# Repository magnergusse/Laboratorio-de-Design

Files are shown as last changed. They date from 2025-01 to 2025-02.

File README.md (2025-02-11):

# Laboratorio-de-Design

[PT] Nesta unidade curricular, o objetivo foi a concepção de um braço robótico para uma missão espacial, cuja definição, incluindo objetivos, requisitos e métricas envolvidas, foi proposta pelo grupo. O projeto CAD do braço robótico foi desenvolvido e concluído com sucesso.

[EN] In this course, the objective was to design a robotic arm for a space mission, with the mission details, including objectives, requirements, and involved metrics, proposed by the group. The CAD design of the robotic arm was developed and successfully completed.

<h2>Gallery</h2>
<p align="center">

<table>
  <tr>
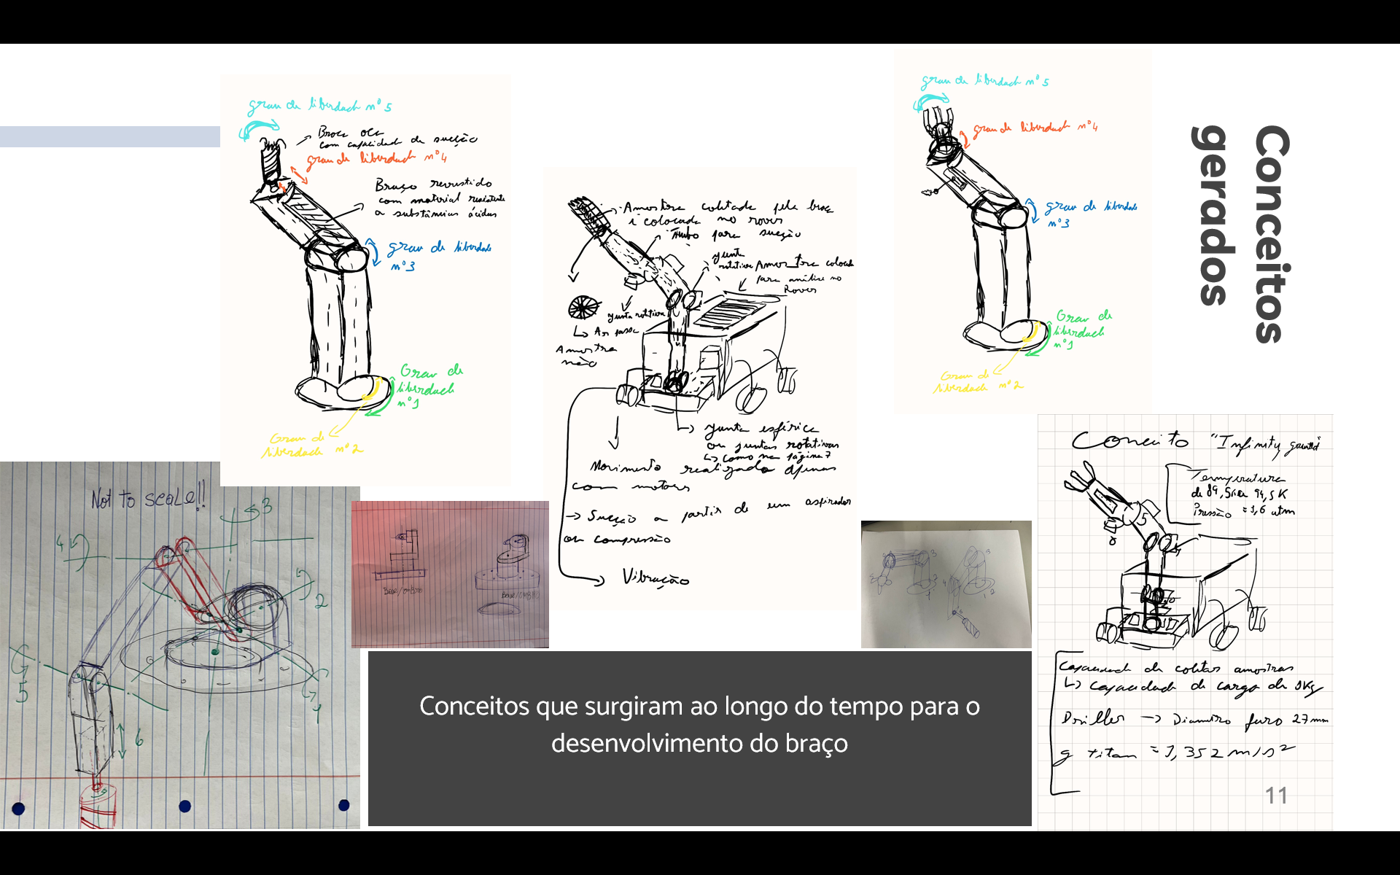
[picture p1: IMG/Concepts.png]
    <td></td>
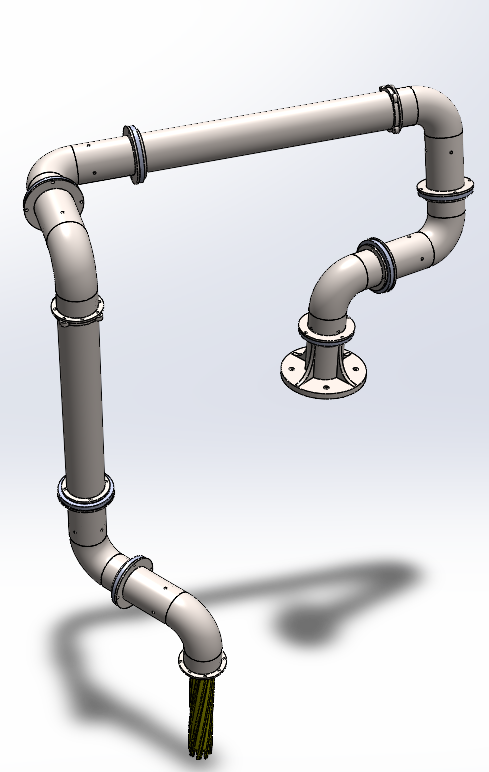
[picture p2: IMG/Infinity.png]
    <td rowspan="2"></td>
  </tr>
  <tr>
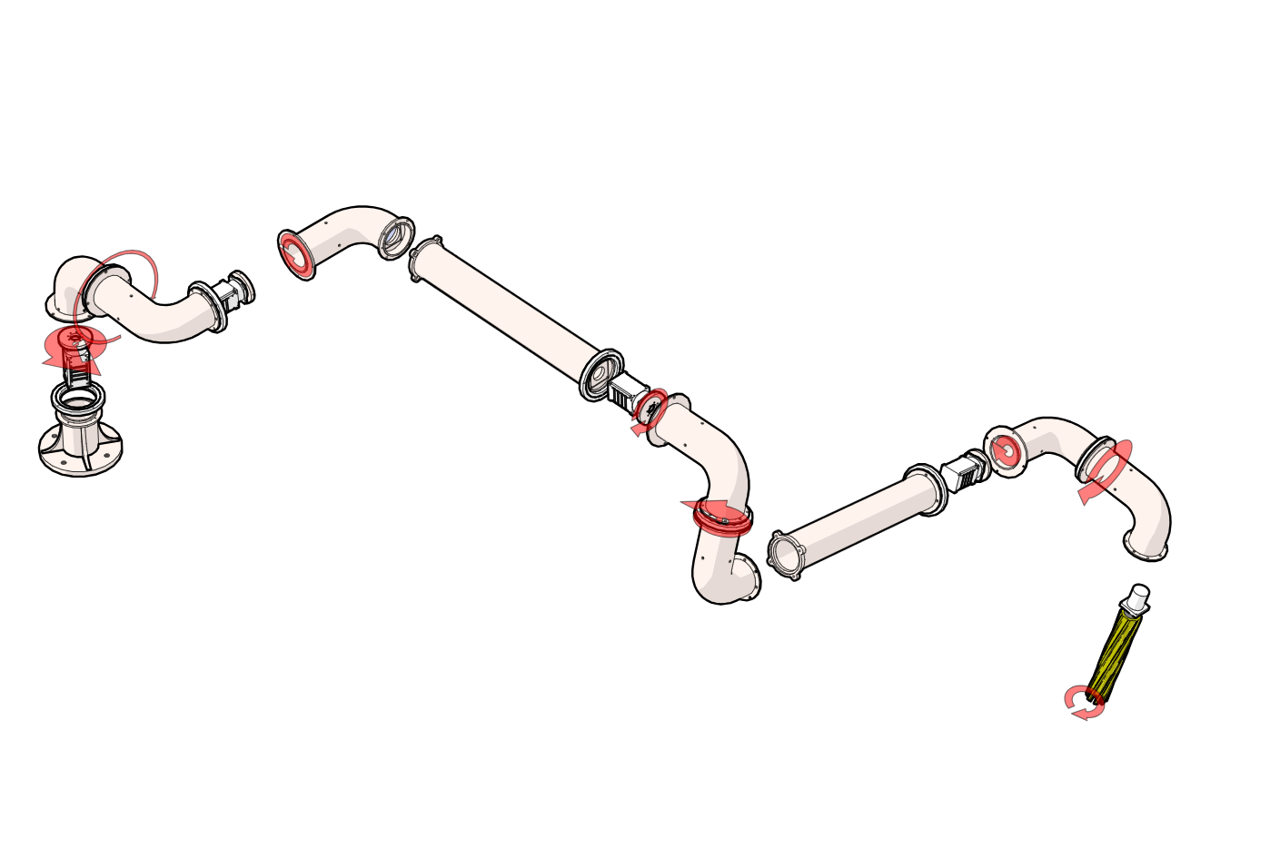
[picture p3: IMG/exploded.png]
    <td></td>
  </tr>
</table>
</p>

<p align="center">
<table>
  <tr>
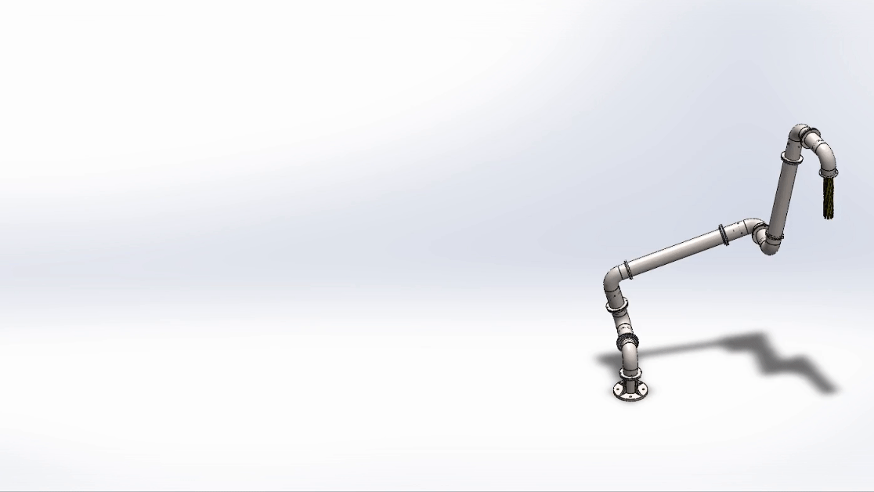
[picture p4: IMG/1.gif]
    <td></td>
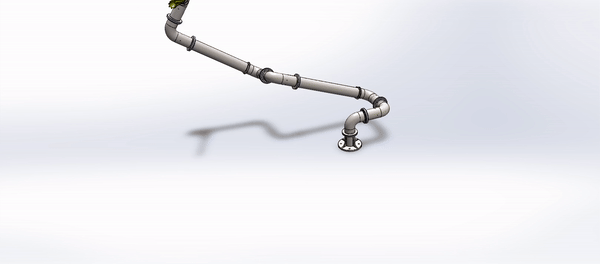
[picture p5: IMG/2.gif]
    <td></td>
  </tr>
<tr>
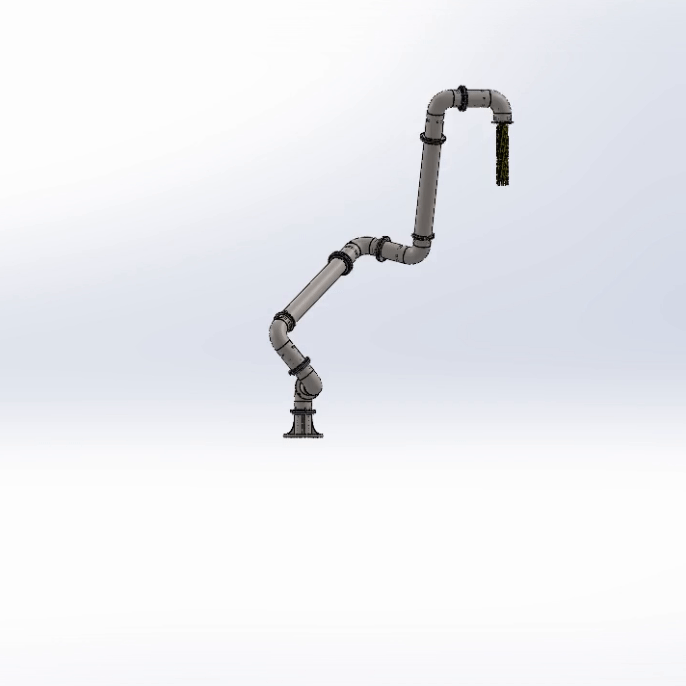
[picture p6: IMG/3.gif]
    <td></td>
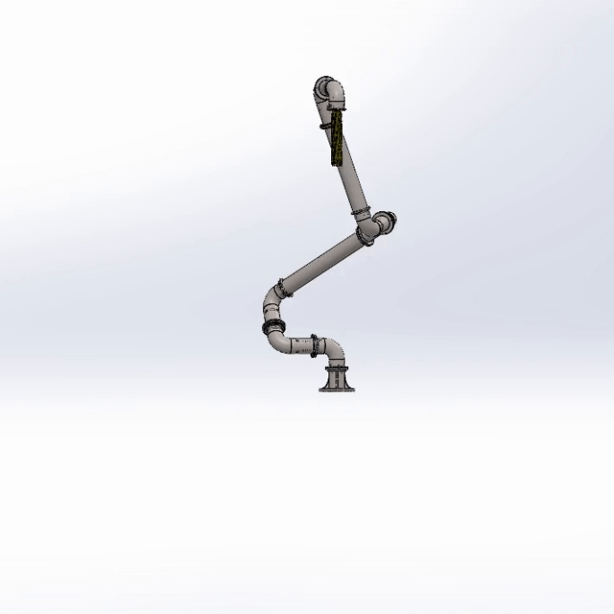
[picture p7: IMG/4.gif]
    <td></td>
</tr>

</table>

 </p>

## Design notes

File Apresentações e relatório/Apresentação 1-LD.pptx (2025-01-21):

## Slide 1

Braço Robótico: Infinity Gauntlet

Apresentação 1
17/10/2023

Grupo:
108217 – Diogo Ribeiro
110180 – Magner Gusse

## Mission Statement

Product description:
- Braço robótico com capacidade de furar o solo e fazer um pick & collect em titã.
Key Goals:
- Estudo da possibilidade de colonização do planeta, mineração do planeta.
Primary Market:
- Comunidade científica.

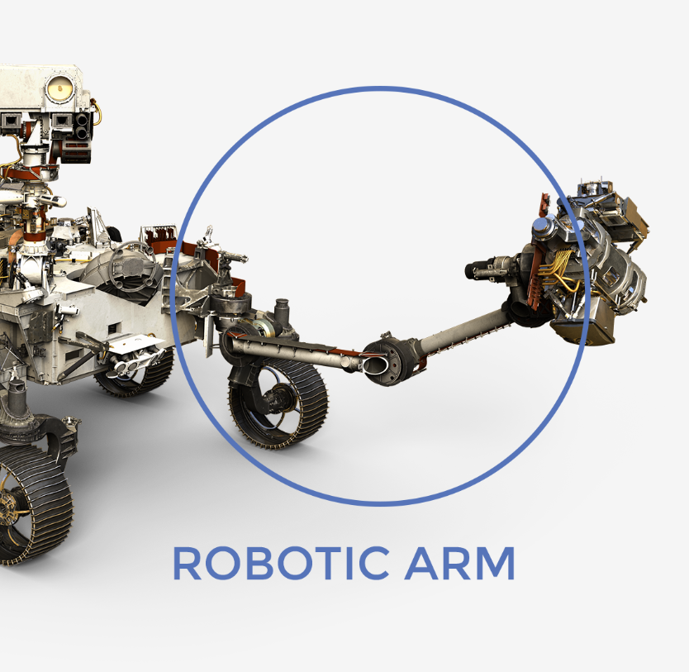
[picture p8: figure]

## Mission Statement

Secondary Markets:
- Comunidade geral.
- Empresas energéticas
Assumptions:
- Resistir às propriedades climatéricas de Titã.
- Acoplavél ao Rover.
- Recorre a mesma fonte energética do Rover.
- 5 graus de liberdade.
- Capaz de fazer furos e coletar amostras.

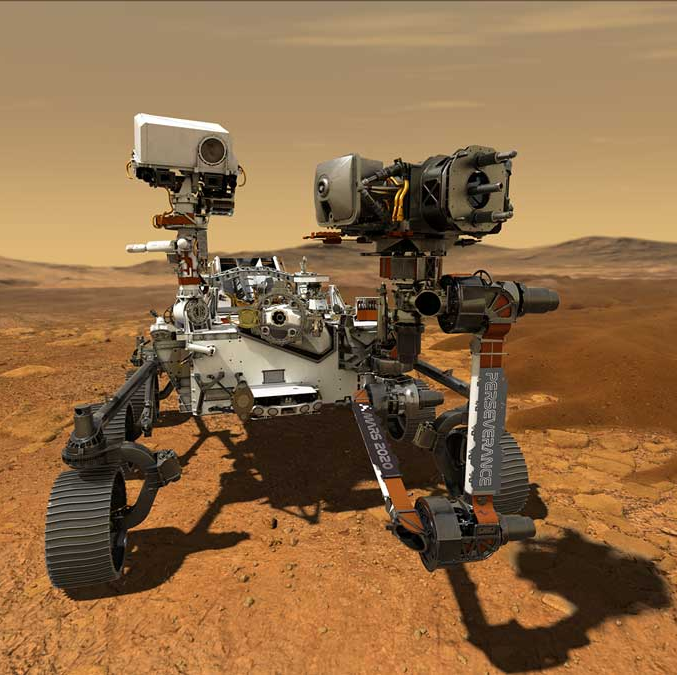
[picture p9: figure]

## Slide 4

Requisitos e especificações

Requisitos | Especificações
Acoplamento ao Rover simples | Feito em 30 minutos
Controlo Remoto | Ligação a 1,2 milhões de quilómetros da Terra
Resistência às propriedades climatéricas | Temperaturas entre 89,5 K e 94,5K
Resistência à pressão atmosférica | Pressão atmosférica de 1,6 atm
Coleção de amostras | Capacidade de carga de pelo menos 3 Kg
Furar a superfície | Furos de 40 mm de diâmetro e 70mm de profundidade
Adapta-se ao campo gravítico | Titã apresenta uma aceleração gravítica de 1,352 m/s²
Capacidade de realizar várias operações | 5 graus de liberdade
Duração total | Tempo de vida de 10 anos
Necessidade de pouca manutenção | Manutenção apenas uma vez ao fim de 5 anos

## Geração de Conceitos

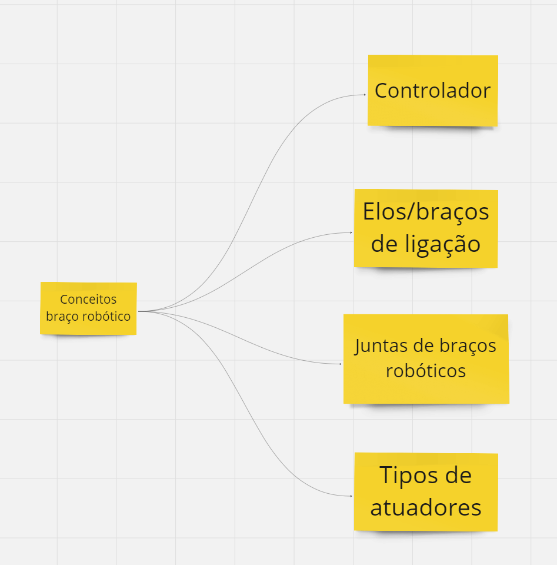
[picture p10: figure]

## Controladores

- Controladores Industriais
- Robustos e Confiáveis
- Suportam cargas pesadas
- Resistentes a Condições ambientais adversas
- Controladores de motores elétricos
- Correspondem a nossa necessidade de alto desempenho

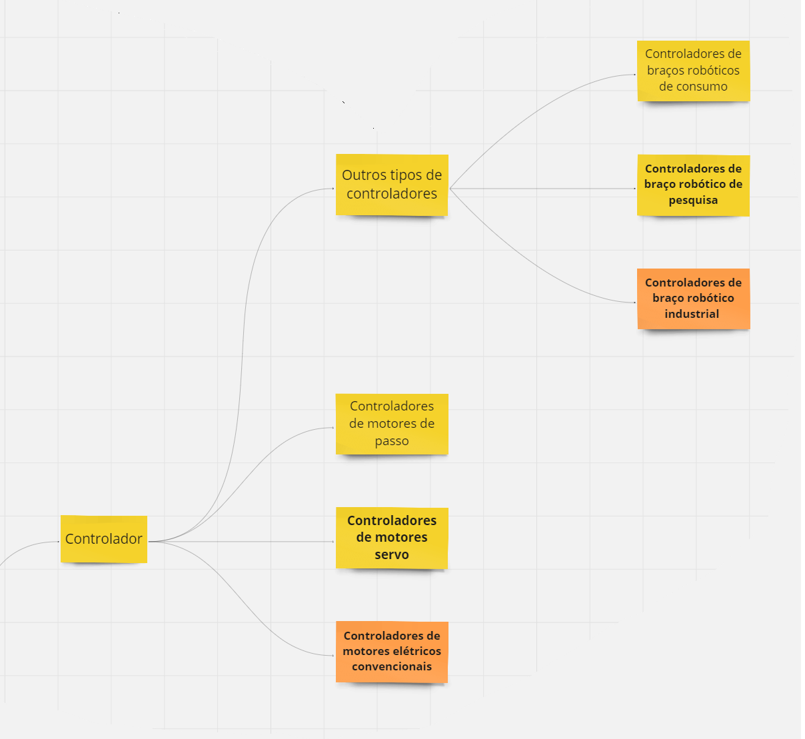
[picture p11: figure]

## Elementos de Ligação

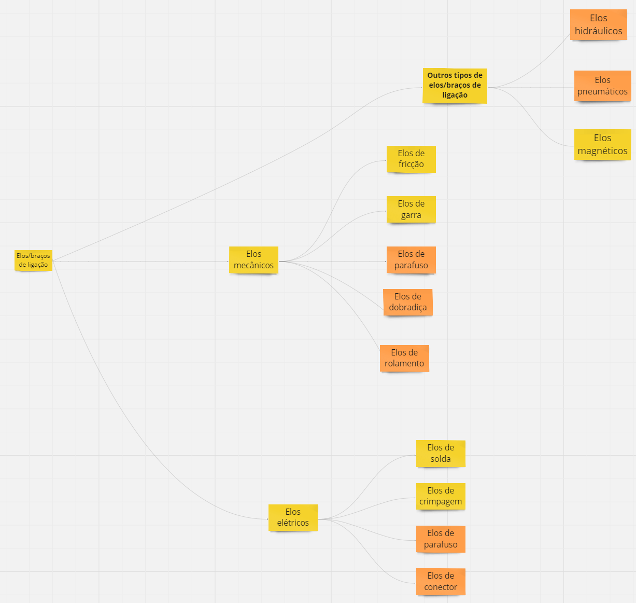
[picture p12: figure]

- Elementos de ligação
- Elos hidráulicos respondem à necessidade de um torque alto
- Elos pneumáticos fornecem um movimento rápido e preciso
- Elos de parafuso fazem a ligação entre vários componentes
- Elo de dobradiça é usado na porta do housing da perfuradora
- Elos de rolamento são usados para o movimento dos diversos componentes do braço
- Elos de conector tratam da ligação entre os diversos componentes elétricos

## Juntas de Braços robóticos

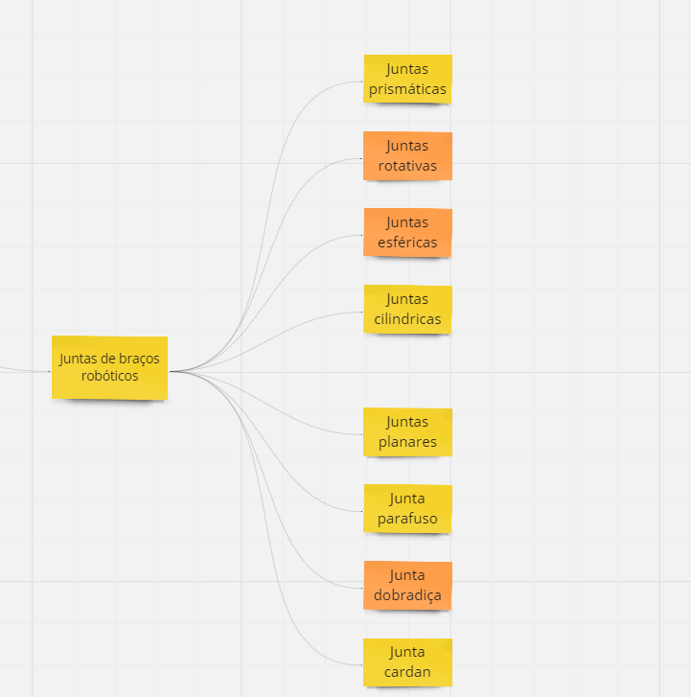
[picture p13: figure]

- Permitem que os braços se movam em várias posições de acordo com o tipo de movimento desejado.

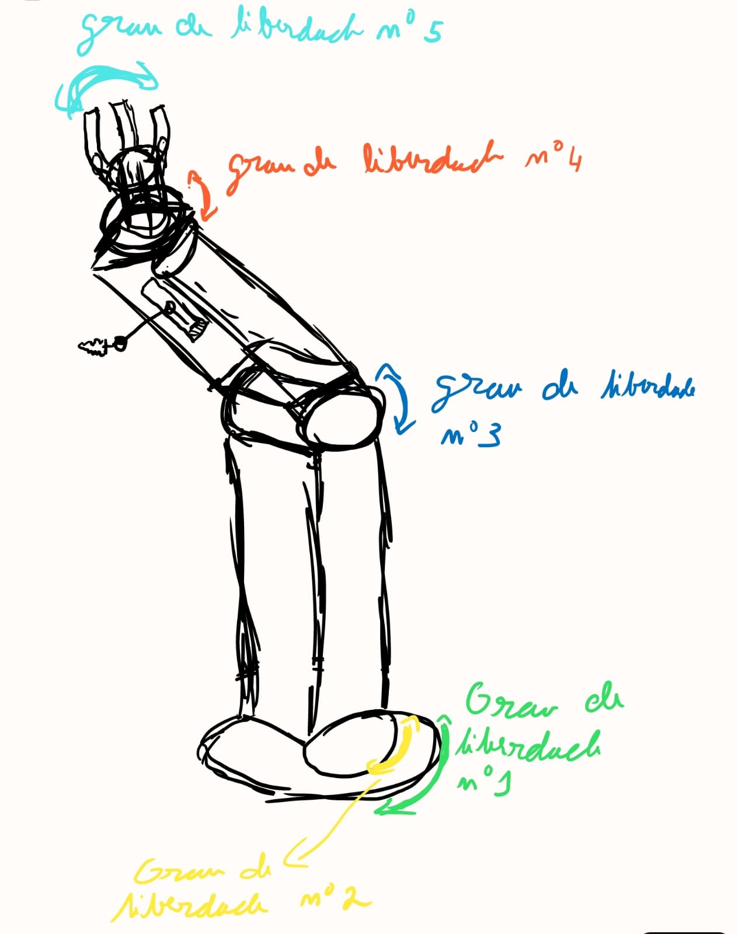
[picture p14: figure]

## Atuadores do Braço robótico

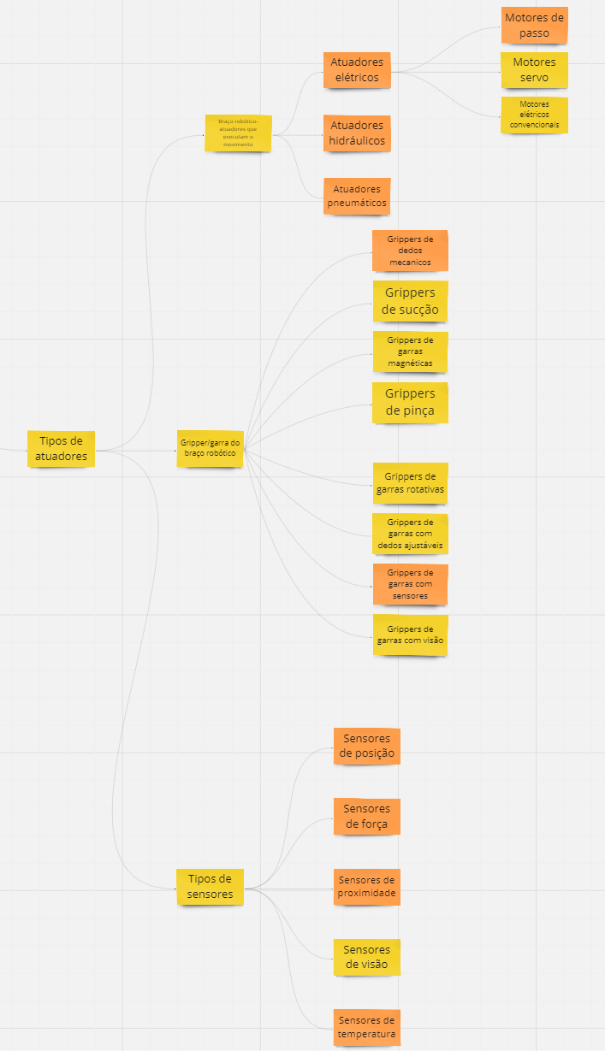
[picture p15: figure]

- Permitem-nos atuar sobre os elementos do braço de forma a realizar os movimentos necessários para o braço realizar as tarefas necessárias.

## Obrigado!

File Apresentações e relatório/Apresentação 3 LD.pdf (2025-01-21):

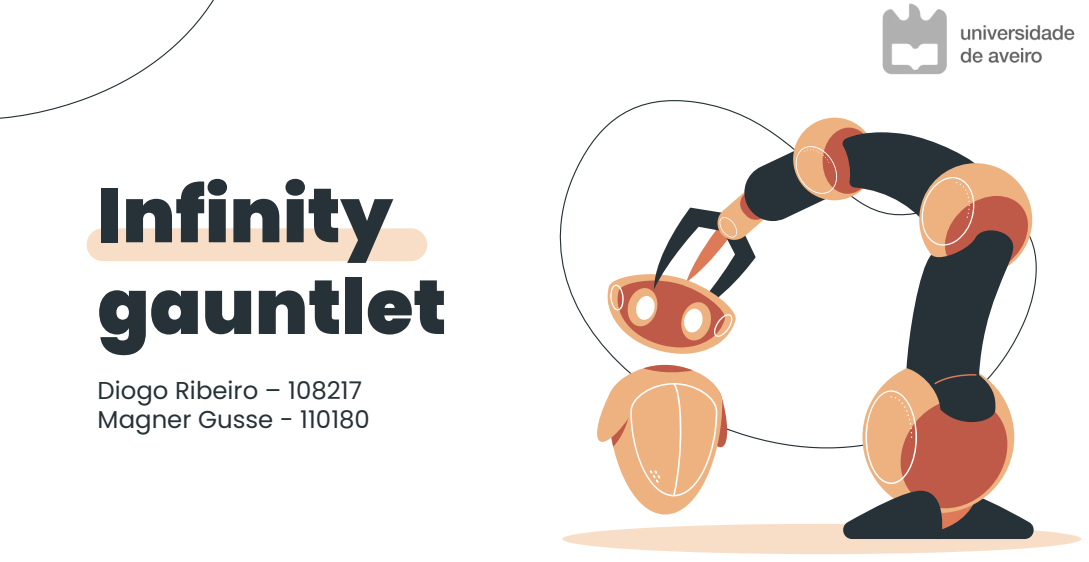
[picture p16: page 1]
Infinity gauntlet; Diogo Ribeiro – 108217 Magner Gusse - 110180

# Assuntos a apresentar

### Objetivos da missão 1 Mission statement e

requesitos a cumprir no
projeto

3

### Conceito escolhido

Apresentação do CAD do
braço e dos seus varios
componentes
4

### Next steps

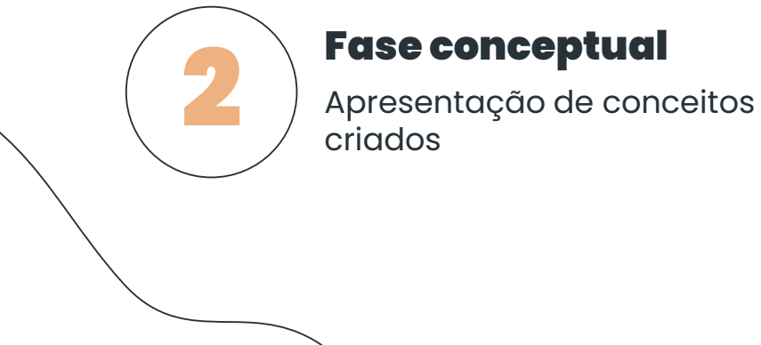
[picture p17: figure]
Fase conceptual Apresentação de conceitos criados

Objetivos a cumprir na fase 2

de prototipagem

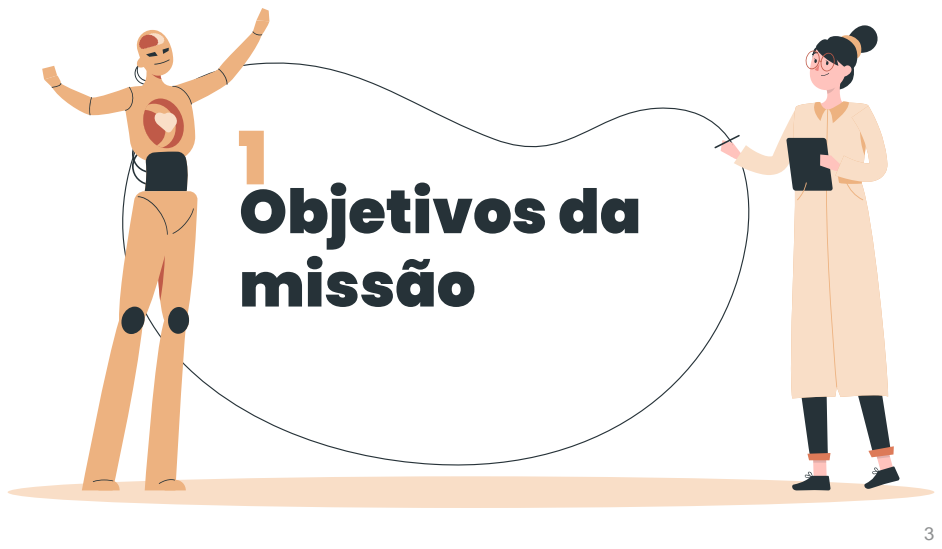
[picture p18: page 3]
Objetivos da missão

# Mission statement

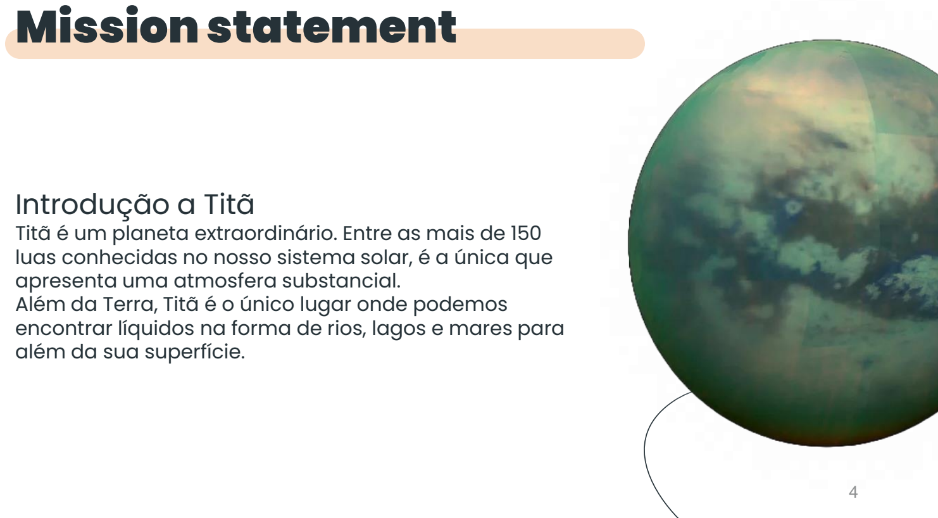
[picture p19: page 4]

## Introdução a Titã

Titã é um planeta extraordinário. Entre as mais de 150 luas conhecidas no nosso sistema solar, é a única que apresenta uma atmosfera substancial.
Além da Terra, Titã é o único lugar onde podemos encontrar líquidos na forma de rios, lagos e mares para além da sua superfície.

# Mission statement –Principais caracteristicas de Titã

### Habitabilidade

Estudos indicam que
Titã é dos planetas mais
habitáveis do Sistema
Solar.

### Condições atmosfericas e climatericas

A atmosfera desta lua é tão densa que um fato de pressão não seria necessário. No entanto é necessário ter atenção às temperaturas extremamente baixas.

### Constituição quimica

Estudo dos elemento
que fazem parte da
composição de Titã

### Mapear a superficie

### Existência de vida

Estudar se já existe
vida em Titã

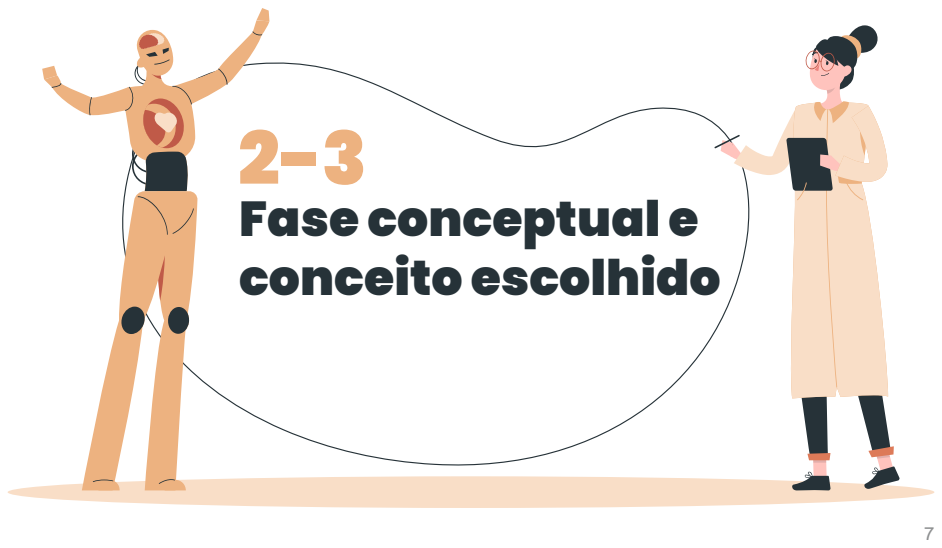
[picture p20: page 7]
Fase conceptual e conceito escolhido

# Project Timeline

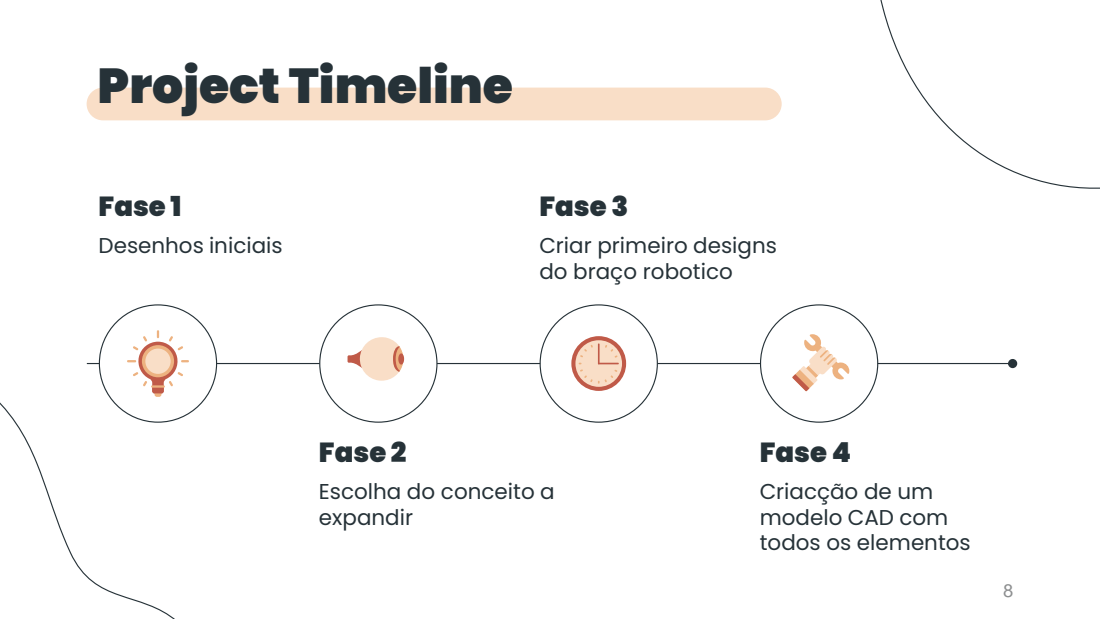
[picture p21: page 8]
Fase 1 Desenhos iniciais

Fase 3
Criar primeiro designs
do braço robotico

Fase 2
Escolha do conceito a
expandir

Fase 4
Criacção de um
modelo CAD com
todos os elementos

# Geração de conceitos-benchmarking

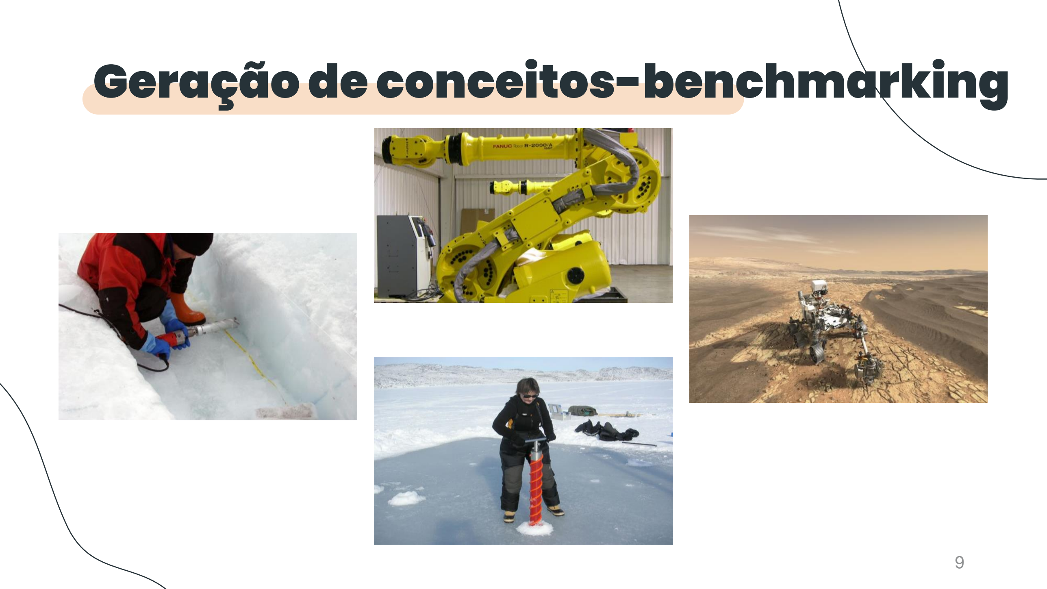
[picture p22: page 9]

Acoplamento simples

Resistencia às condições
Temperaturas entre 89,5 K e 94,5K e substancias ácidas

Acoplamento feito em
30 minutos

# Desenhos iniciais

### Controlo remoto

Controlado pela ground
station na Terra

### Adaptação à gravidade

Aceleração gravítica com
um valor de 1,352 m/s²

Antes de fazer qualquer desenho é necessário saber quais requisitos o braço deve ser capaz de cumprir.

# Desenhos iniciais

### 1º desenho

Braço robótico com um gripper para recolha de amostras de gelo

Porém tivemos de largar esta ideia pois um gripper e recolha de amostras de gelo saõ incompativeis.

# Escolha de um conceito

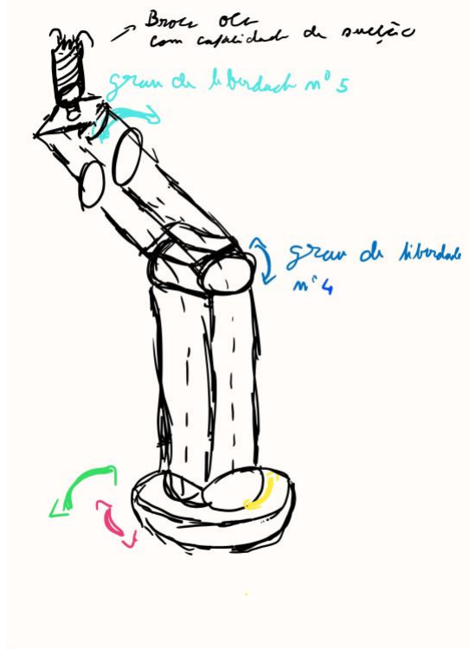
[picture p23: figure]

Após reconsideração foi decidido
usar um braço robótico com uma
broca oca na sua ponta para uma recolha de amostras.
O conceito escolhido apresentaria 5 graus de liberdade.

# Primeiros designs

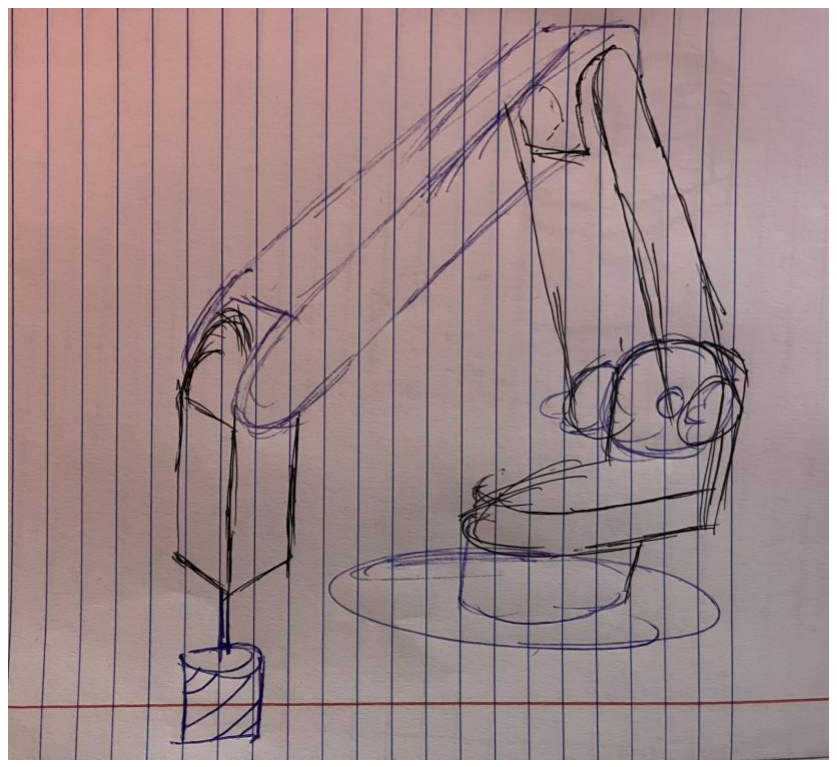
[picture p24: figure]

Tendo em conta o conceito
selecionado foi iniciado o primeiro
design.
Este design foi feito para um braço com 1200 mm de comprimento.
O braço usaria motores servos para o seu movimento exceto na broca onde se usaria um brushless motor.

# Componentes e modelo

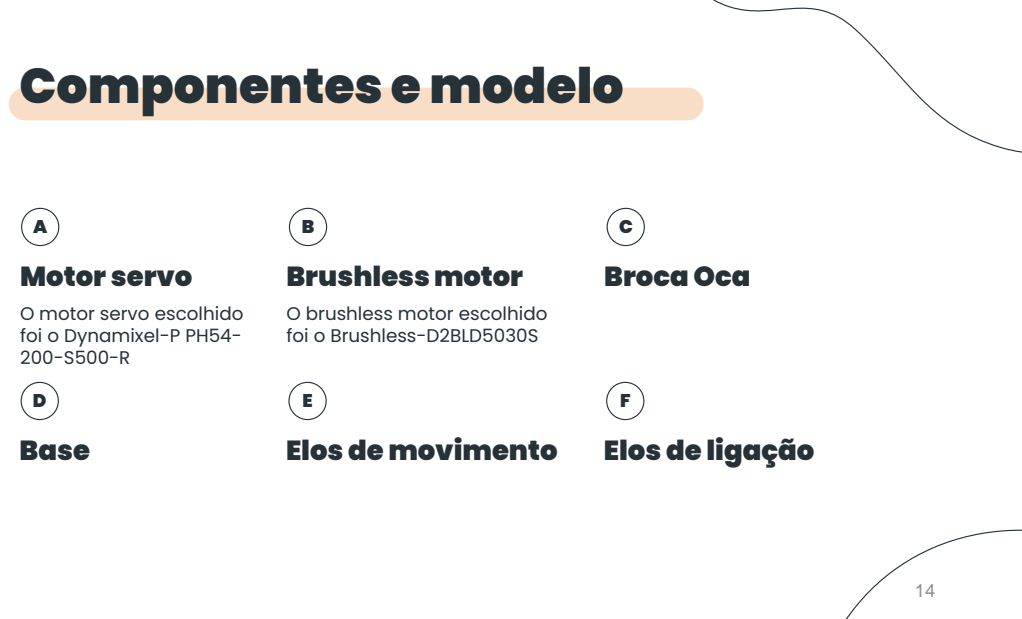
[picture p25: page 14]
Motor servo; O motor servo escolhido foi o Dynamixel-P PH54- 200-S500-R; Broca Oca; Base

Brushless motor
O brushless motor escolhido
foi o Brushless-D2BLD5030S

Elos de movimento

Elos de ligação

características e dimensões: -Torque control -Velocity control -Position control -Extended position control -PWM control (voltage control

-Peso: 0,855 kg -Dimensões: 54 x 126 x 54 mm A

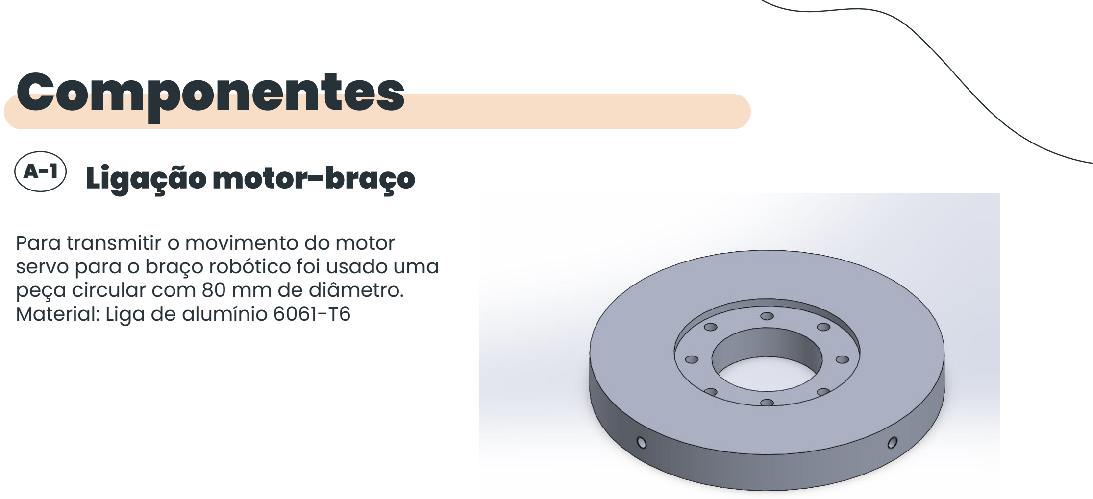
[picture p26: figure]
Ligação motor-braço; Para transmitir o movimento do motor; peça circular com 80 mm de diâmetro. Material: Liga de alumínio 6061-T6; Componentes

servo para o braço robótico foi usado uma

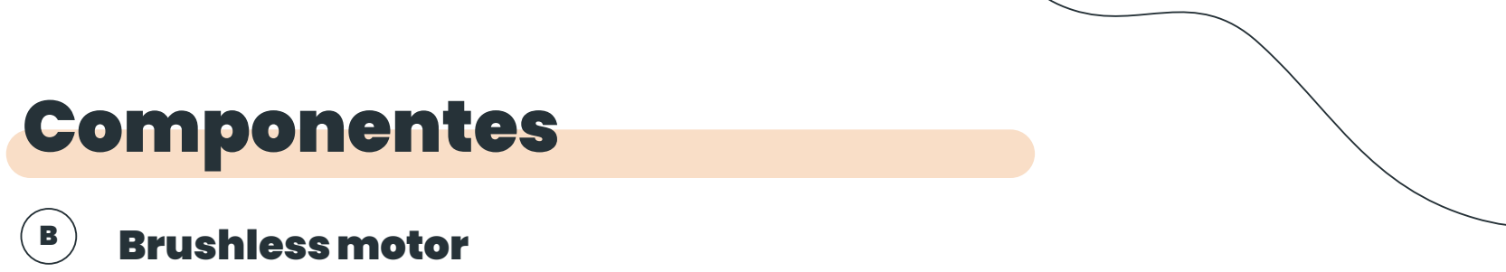
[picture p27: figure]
Brushless motor; Componentes

O brushless motor escolhido foi o Brushless-D2BLD5030S Este apresenta as seguintes características e dimensões:
-Velocidade de rotação: 3000 rpm
-Peso do motor: 2 Kg
-Potência requerida: 0,05 kW -Dimensão A: 50 mm
-Dimensão B: 50 mm

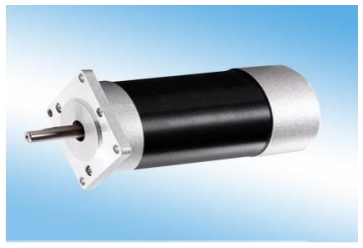
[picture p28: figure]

### Broca Oca

# Componentes

A broca oca escolhida
apresenta as seguintes
dimensões:

C

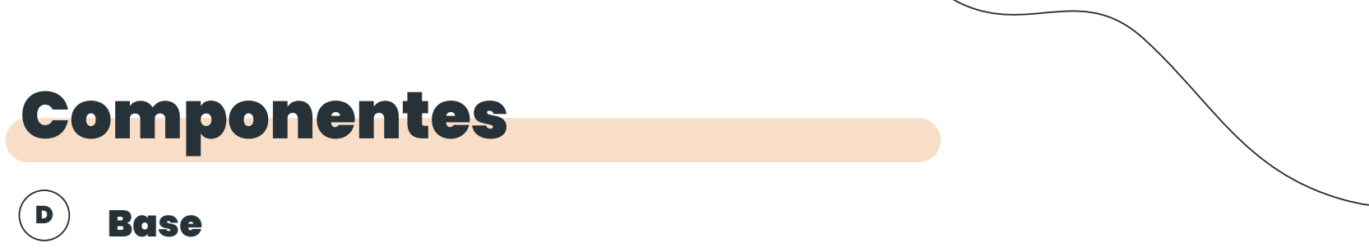
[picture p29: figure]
Base; Componentes

A base para o nosso braço robótico é composta por 3 componentes que são ligados entre si por soldadura. Esses 3 componente são: -A parte inferior circular com 200 mm de diâmetro, sendo esta feita a partir de um processo de maquinagem -A parte cilíndrica com 87 mm de diâmetro, que seria feita a partir de um processo de extrusão -As “ribs”, que também são feitas a partir de um processo de

# maquinagem D

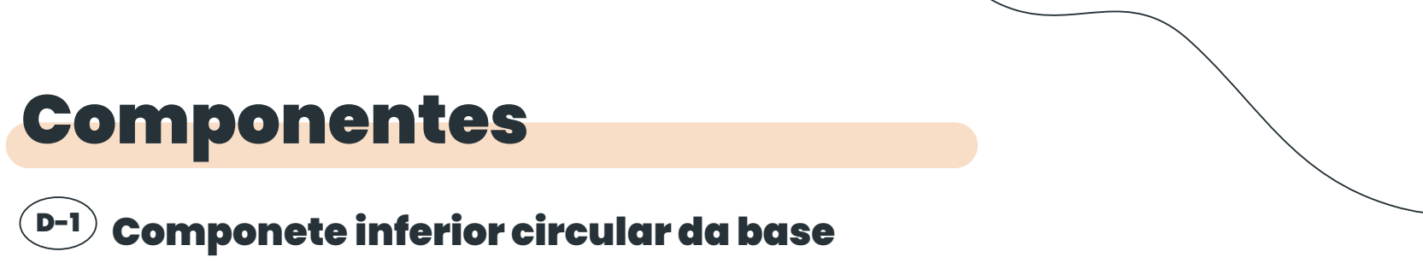
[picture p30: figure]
Componete inferior circular da base; Componentes
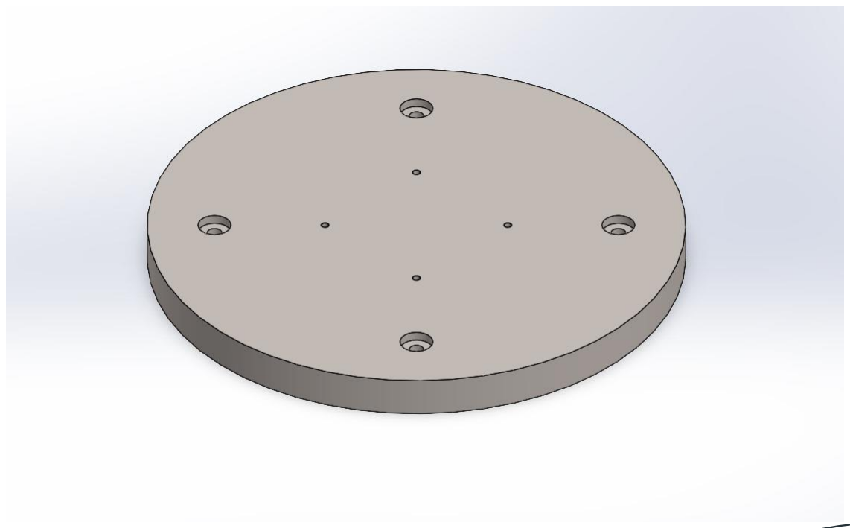
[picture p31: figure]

-A parte inferior circular com 200 mm de diâmetro, sendo esta feita a partir de um processo de maquinagem

Ribs de ligção; -As “ribs”, que também são feitas a partir de um processo de maquinagem; Componentes

Processo de fabrico: Flexão por indução a calor

Elos para ligação; Material: Liga de Titânio Ti-6AI-4V Processo de fabrico: Extrusão; Componentes

Modelo CAD do braço robótico; Primeiro motor

Modelo CAD do braço robótico; Terceiro Motor

Modelo CAD do braço robótico; Elo 2 e quinto motor

Modelo CAD do braço robótico
Next Steps

Obrigado! Questões?

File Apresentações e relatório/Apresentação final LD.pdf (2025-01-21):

Diogo Ribeiro – 108217
Magner Gusse - 110180


# Braço robótico:

# Infinity Gauntlet

Assuntos a tratar

Fase conceptual e conceito 03 | escolhido

Sobre a missão

Breve descrição sobre a missão 01 | em que pretendemos embarcar

Requisitos a cumprir

Requisitos que o braço deve 02 | cumprir para esta missão

Apresentação do braço, dos seus componentes e o seu
uso
Especificações do produto,
soluções técnicas e construtivas, material, desenhos e uso

04

Conclusões

O que fazer a seguir com este 05 | projeto

## Sobre a missão:

O projeto do desenvolvimento do braço robótico foi realizado para a missão de exploração da lua de Saturno Titã

Titã?
Porquê escolher

Titã é um planeta extraordinário. Entre as mais de 150 luas conhecidas no nosso sistema solar, é a única que apresenta uma atmosfera substancial.
Além da Terra, Titã é o único lugar onde podemos encontrar líquidos na forma de rios, lagos e mares para além da sua superfície.

As características mais relevantes de Titã são a sua possivel habitabilidade e as suas condições atmosféricas e climatéricas

-Constituição química
-Mapeamento da superfície
-Existência de vida

Principais
caracteristicas

Assuntos a estudar na
missão

Introdução a Titã

## Requisitos a


## cumprir

02

cumprir; Requisitos a

Acoplamento
simples
Acoplamento feito em 30
minutos

Controlo
Remoto
Equipamento controlado na
ground station na Terra

Resistência às
condições
Equipamento resistente
às temperaturas entre
substâncias ácidas

Adaptação ao
campo gravitico
Aceleração gravítica com um
valor de 1,352 m/s

BUDGET

Transporte até
Titã

Rover

Braço robótico

60%

30%

10%

## Fase conceptual e conceito


## escolhido

03

Recolha de informações sobre braços robóticos e ganho de conhecimento sobre os mesmos.
Fase de ganho de conhecimento sobre os aspetos mais importantes do projeto.

Benchmarking


Braço robótico com um gripper para recolha de amostras de gelo.
Porém tivemos de largar esta ideia pois um gripper e recolha de amostras de gelo são incompatíveis.

conceito

Primeiro


Conceitos que surgiram ao longo do tempo para o desenvolvimento do braço

gerados

Conceitos

Após reconsideração foi decidido usar um braço robótico com uma broca oca na sua ponta para uma recolha de amostras.
O conceito escolhido apresentaria 5 graus de liberdade.

escolhido

Conceito


Modelo que serviu de inspiração de filosofia no desenvolvimento do projeto.
Modelo UR10e da Universal Robots por apresentar dimensões próximas do idealizado para o Infinity Gauntlet.

inspiração

Modelo de

Apresentação do
braço, dos seus
componentes e o seu
uso

04

brushless

Motor Servo e

motor

O motor servo foi o primeiro componente a ser


escolhido, pois é o componente critico para o dimensionamento do raio do nosso braço robótico. O motor servo escolhido foi o Dynamixel-P PH54-200-S500-R e este apresenta características como:

- Torque control
- Velocity control
- Position control
- Extended position control
- PWM control (Voltage control)
- Peso de 0,855 Kg
- Dimensões de 54 x 126 x 54 mm

De seguida foi escolhido um brushless motor

para o movimento da broca, o escolhido foi o Brushless-D2BLD5030S e este apresenta as seguintes características:

- Velocidade de rotação maxima de 3000 rpm
- Peso do motor de 1,200 Kg
- Potencia requerida de 0,05 kW
As dimensões deste motor estão apresentadas na seguinte imagem:

movimento motor

Peça para transmissão do


-braço

Para transmitir o movimento do motor servo para o braço robótico foi usada uma placa transmissora com um diâmetro de 80 mm o que permite o direct-drive.
Mais especificamente o material usado foi a Liga de titânio Ti-6Al-4V Este componente é feito a partir do processo de maquinação.

facilitar rotação
Rolamento usado para
Escolhido o Crossed Roller Bearing por resistir a forças axiais, radiais e momentos. Apresentando fixações aparafusadas aos anéis fixo e móvel.


facilitar rotação
Rolamento usado para
Para evitar desgaste de peças por atrito durante a rotação devido ao atrito entre os vários componentes foi desenvolvido um modelo simplificado do rolamento Crossed Roller Bearing.


de amostras

Broca oca para coleção
A seguir foi criada a broca para a coleção de amostras. Esta apresenta as dimensões que podemos ver na imagem e foi feita a partir de Titânio.

para o braço robótico

Escolha de material
A escolha do material do braço robótico consistiu em 5 fases de filtragem, sendo essas varias fases requisitos que o material deve cumprir, este processo foi feito com recurso ao software Granta-Edupack.

para o braço robótico

Escolha de material
O primeiro critério aplicado foi a necessidade do material apresentar uma temperatura de serviço mínima inferior a 89,5 K. Isso baixou o numero de opções de 4243 para 1625.


para o braço robótico

Escolha de material
O segundo critério aplicado foi a resistência a substancias acidas, onde neste estudo foram escolhidas substancias que apresentam uma resistência aceitável ou excelente. Isso baixou o numero de opções para 1143.

para o braço robótico

Escolha de material
O terceiro critério considerado foi se o material usado pode ser usado em processos de fundição. Para isso foram escolhidos materiais que apresentam uma performance aceitável ou excelente neste índice. Isto baixou o número de opções para 184.


para o braço robótico

Escolha de material
O quarto critério em consideração foi a tensão de cedência. Neste caso recolhemos apenas os materiais que se apresentassem numa posição superior a uma reta definida num gráfico densidade- tensão de cedência. Isto baixou o numero de opções para 89.


para o braço robótico

Escolha de material
Por ultimo tivemos em consideração a condutividade térmica, algo importante para a proteção de componentes. Foram apenas escolhidos materiais que possuíam uma condutividade térmica superior a 10 W/m.ºC. Isto baixou o numero de materiais possíveis para apenas 19.

para o braço robótico

Escolha de material
Dentro dessas 19 opções temos ligas de níquel e ligas de titânio, porem como as ligas de titânio apresentam uma massa menor para uma performance mecânica semelhante escolhemos entao no final como material: Titanium, alfa-beta alloy, Ti-6Al-4V cast.


O braço robótico apresenta inúmeros componentes.
robótico

Componentes do braço

Mas primeiro vamos apresentar a base que se divide numa plataforma circular e um cilindro para conter o motor. Estes componentes são feitos a partir do processo de fundição e maquinação.

robótico

Componentes do braço
A seguir temos a ligação “cotovelo”, a principal parte para a rotação do braço. Nesta ligação também temos um diâmetro interior de 87 mm. Todos os componentes que fazem parte desta ligação são feitos a partir do processo de fabrico de fundição e maquinação.


Montagem das peças móveis
Ilustração da montagem das peças móveis, processo este que é repetido ao longo do braço.


robótico

Componentes do braço
Por último, temos o elo de ligação mais longo que permite termos um raio de funcionamento favorável. Este elo é usado duas vezes no braço robótico, apresenta 87 mm de diâmetro exterior. É fabricado a partir de fundição e maquinação.


robótico

Componentes do braço

Design for Assembly

Separação da base para permitir montagem do motor por ligação aparafusada.


robótico

Componentes do braço

Design for Assembly

Criação de bases e furos para fixação e montagem dos
rolamentos nos diferentes componentes de interação. | 32


robótico

Componentes do braço

Design for Manufacturing

Peças com perfil que permite a separação do macho de areia em processos de fundição.


robótico

Componentes do braço

Design for Manufacturing

Peças com pelo menos 1 plano de simetria para maior facilidade de fabrico em fundição

robótico

Componentes do braço

Design for Manufacturing and Assembly

Adição de filets para remoção de arestas vivas e acomodação das limitações do fabrico.


robótico

Visão geral do braço
O braço robótico completo apresenta as seguintes características:
- Massa de 25 Kg
- 7 graus de liberdade
- Capacidade de carga de 5 Kg
- Raio de serviço entre 1m e 1,5m.
- Comprimento total de 1.6 m
- Material usado- Liga de titânio Ti-6Al-4V cast.

braço

Funcionamento do
Demonstração funcional da mobilidade do braço.


funcionamento
Demonstração de
Demonstração funcional da perfuração do solo, conseguindo chegar a 1.2m abaixo do nível da base

## Conclusões

05


Estamos abertos a quaisquer questões que tiverem.

## Obrigado!

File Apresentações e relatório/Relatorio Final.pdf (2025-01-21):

### Universidade de Aveiro

# Relatório de trabalho – Braço robótico Infinity Gauntlet

# Laboratório de Design

Autores:

### Diogo Ribeiro – 108217 Magner Gusse - 110180

Data:

### 17 de Janeiro 2024

# Índice

Especificações finais do braço robótico | Error! Bookmark not defined.
Conclusões | Error! Bookmark not defined.

Introdução

Este projeto foi realizado no âmbito da cadeira de laboratório de design. Este projeto foi apresentado como a criação de um braço robótico para uma missão espacial à escolha dos alunos, onde o braço robótico do Rover de exploração de marte Perserverance serviu como inspiração.
O lugar escolhido pelo nosso grupo para o projeto foi uma das luas de Saturno, Titã. Titã foi escolhido como alvo de uma missão de um estudo da constituição química e mapeamento do mesmo.
O nosso braço robótico seria então focado estritamente na recolha de amostras para estudo da constituição química de Titã.

Mission Statement

Então esta missão consistiria no envio de um rover com um braço robótico para Titã, sendo o braço focado numa capacidade de drill & collect de amostras.
O objetivo deste estudo seria analisar a possibilidade de colonização do planeta ou mineração do planeta.
Os principais interessados neste estudo/missão são a comunidade científica e o alvo secundário seria a comunidade geral e as empresas energéticas.
Esta missão teria no total um custo entre 800 e 1000 milhões de dólares, sendo que esta missão tem um início planeado em 2028 e chegada a Titã em 2034.

Requisitos e especificações

Primeiro é necessário definir alguns critérios que o braço robótico tem de ser capaz de satisfazer, esses são:
- Acoplamento fácil ao Rover:
- Acoplamento feito em apenas 30 minutos.
- Capacidade de controlo remoto
- Controlo feito na ground station na Terra.
- Resistência às condições de Titã
- Resistência a temperaturas muito baixas entre 89,5 K e 94,5 K e à existência de substâncias acidas.
- Adaptação ao campo gravítico:
- Aceleração gravítica de Titã com um valor de 1,352 m/s².
- Capacidade de realizar várias operações:
- Pelo menos 5 graus de liberdade.
- Perfurar a superfície de gelo:
- Coleção de amostras de gelo.
- Duração total:
- Tempo de vida de 10 anos.

Geração de conceitos

Sabendo que o braço era destinado a realizar funções de pick & collect foi criado um primeiro conceito que consistia num braço robótico com 5 graus de liberdade que apresentava um gripper para recolha de amostras na sua ponta.


Fig.1 Conceito inicial
Porém como a recolha vai ser apenas de amostras de gelo, chegamos á conclusão de que este primeiro conceito é incompatível com a recolha dessas mesmas amostras pretendidas, por isso foi criado outro conceito com uma broca oca na ponta do braço robótico.


Fig.2 Conceito melhorado

Desenvolvimento – Primeiro design

Tendo em conta o conceito selecionado foi iniciado o primeiro design. Este design foi feito para um braço com 1200 mm de comprimento. O braço usaria motores servos para o seu movimento exceto na broca onde se usaria um brushless motor.
O nosso braço robótico foi inspirado na linha de braços robóticos UR da universal robots e a tecnologia da broca oca foi inspirada na chipmink drill.


Fig.3-Modelo da Universal Robots Fig.4- Modelo de broca oca

Então foi feito um primeiro desenho para o nosso braço robótico:


Fig. 5- Desenho inicial

Material escolhido para o braço robótico

A fase seguinte consistia em escolher um material para o braço robótico. A escolha deste material foi feita a partir do software Granta-Edupack, sabendo os requisitos que o nosso braço precisava de cumprir.
Esses requisitos são:

Temperatura de serviço mínima inferior a 89.5 K: Após este primeiro passo reduz-se o número de possíveis opções de 4243 para 1625.


Fig.6-Etapa 1 da escolha de material

Resistência a substâncias ácidas: Foi definido que para este projeto apenas poderiam ser usados materiais que apresentassem uma resistência aceitável ou excelente a substâncias ácidas. Isto baixou o número de possíveis opções para 1143.


Fig.7-Etapa 2 da escolha de material

Materiais apropriados para fundição: O processo de fabrico mais apropriado para este tipo de projeto é a fundição e para isso o nosso material tem de ser apropriado para o mesmo. Para isso foi definido aceitar apenas materiais que apresentassem ser apropriados a um nível aceitável ou excelente. Isso baixou o número de possíveis opções para 184.


Fig.8-Etapa 3 da escolha de material

Tensão de cedência: De seguida foi feito um estudo para obter materiais que apresentavam uma posição superior a uma reta definida num gráfico densidade-tensão de cedência. Isso baixou o número de opções para 89.


Fig.9-Etapa 4 da escolha de material

Condutividade térmica: Por último, foi feito um estudo para determinar os materiais que possuíam uma condutividade térmica superior a 10 W/m.ºC, sendo este um critério importante para a proteção de componentes. Isso baixou o número de opções para apenas 19.


Fig.10-Etapa 5 da escolha de material

Dentro dessas 19 opções existem ligas de níquel e ligas de titânio, porem como as ligas de titânio apresentam uma massa menor para uma performance mecânica semelhante foi decidido seguir com as ligas de titânio tendo no final sido escolhido: Titanium, alfa-beta alloy, Ti-6Al-4V cast, pois de entre as ligas restantes, é o mais apropriado para processos de fundição.

A fundição foi o processo de fabrico escolhido para estes componentes todos devido á sua flexibilidade, visto que permite criar peças de diferentes tamanhos e complexidades e também devido á resistência e durabilidade que as peças criadas por este processo adquirem.

Componentes do braço robótico

A próxima fase consistiu em criar o braço robótico num software CAD, neste caso o SOLIDWORKS, assim sendo os componentes a apresentar seriam alguns adquiridos e outros feitos de raiz.

Motores

Primeiro foram escolhidos o servo motor a usar nos diversos pontos do braço e o brushless motor a usar na broca, estes foram a primeira fase do design do braço pois são extremamente importantes para o dimensionamento do braço em termos de raio e espessura do mesmo.
O servo motor escolhido foi o Dynamixel-P PH54-200-S500-R e este foi escolhido pelas seguintes características:
- Controle de torque.
- Controle de velocidade.
- Controle de posição.
- Controle de voltagem.
- Peso : 0.855 kg.
- Dimensões: 54 x 126 x 54 mm
Este motor é uma excelente opção pois apresenta uma alta performance numa massa baixa e em dimensões favoráveis.


Fig.11-Servo motor

O brushless motor escolhido foi o Brushless-D2BLD5030S, este apresenta as seguintes características e dimensões:
-Velocidade de rotação: 3000 rpm
-Peso do motor: 2 Kg
-Potência requerida: 0.05 kW


Fig.12-Brushless motor

Rolamento

Para evitar o desgaste dos vários componentes devido ao atrito entre os mesmos. Para isso foi usado um rolamento.
O rolamento que foi escolhido foi um Crossed Roller Bearing, pois este é capaz de resistir a esforços radiais, axiais e pequenos momentos. Neste âmbito foi desenvolvido um modelo simplificado deste rolamento, com as dimensões e fixações apropriadas para o braço.


Fig.12 e Fig.13-Rolamento desenvolvido

Broca oca

A seguir foi criada a broca para a coleção de amostras. Esta apresenta as dimensões que podemos ver na imagem e foi feita a partir de Titânio.
Foi escolhido o Titânio devido à sua strenght-weight ratio, resistência a corrosão e resistência a temperaturas baixas.


Fig.14 e Fig.15-Broca oca e desenho técnico da broca.

Além destes, foram desenvolvidas peças de raiz para a estrutura do braço.

Transmissor de movimento

Para ocorrer a transmissão do movimento do motor para o braço foi criada uma peça para esse propósito, transmissão essa que vai ser tipo direct drive. Esta peça é feita de titânio e apresenta uma forma circular com um diâmetro de 80 mm. Mais especificamente o material escolhido foi a Liga de titânio Ti-6Al-4V


Fig.16-Transmissor de movimento


Base

Primeiro foi desenvolvida a base, esta que vai ser a ligação do braço ao Rover que o sustenta. que se divide numa plataforma circular e um cilindro para conter o motor. Estes componentes são feitos a partir do processo de fundição e a ligação entre a plataforma e a parte cilíndrica é feita a partir de soldadura.

Fig.17-Montagem do motor na base

A plataforma circular apresenta furos para a fixação ao Rover e fixação do motor e um diâmetro de 200 mm.

Fig.18-Base fixa ao Rover

A parte cilíndrica apresenta uma parte central para alocação do motor e um diâmetro externo de 87 mm, apresenta ainda uma base com furos para a fixação ao rolamento e ribs para apoio estrutural.


Fig.19-Segunda parte da base

Cotovelos

A seguir temos a ligação “cotovelo”, a principal parte para a rotação do braço. Nesta ligação também temos um diâmetro externo de 87 mm. Esta ligação apresenta vários componentes como o “ombro”, rolamento e motor servo. Sendo que neste ombro temos três componentes sendo esses dois “ombros” podendo ser do mesmo tamanho ou de tamanhos diferentes como é o caso do primeiro que se localiza diretamente acima da base, o motor e o transmissor de movimento. A fixação dos motores é feita numa base no interior do braço que permitem colocar o motor numa posição fixa e aparafusar os motores.
Os “ombros” são também perfurados estrategicamente de forma a aparafusar o transmissor de movimento, os rolamentos e os elos.
Todos os componentes que fazem parte desta ligação são feitos a partir do processo de fabrico de fundição.


Fig.20 e Fig.21-“ombro” e “cotovelo”

Elo

Por último, temos o elo de ligação mais longo que permite termos um raio de funcionamento favorável. Este elo é usado duas vezes no braço robótico, apresenta 87 mm de diâmetro externo e um comprimento de 505.75 mm, contém uma base para fixação de rolamento do motor e outra base para a sua própria fixação.
É fabricado a partir de fundição.


Fig.22-Elo

É importante ainda mencionar que as peças todas além de serem feitas por fundição em moldes de areia, devem ainda passar por maquinação para tratamento dos furos e tratamento superficial das superfícies que entram em contacto com outras peças.

Design for Assembly

Para satisfazer o requisito de montagem em 30 minutos foram tomadas várias decisões durante o design, tais como:
- Separação da base para permitir montagem do motor por ligação aparafusada.
- Criação de bases e furos para fixação e montagem dos rolamentos nos diferentes componentes de interação.
- Adição de filets para remoção de arestas vivas para evitar cortes e lesões.


Fig.23, 24 e 25-Considerações de Design for Assembly


Design for Manufacturing

Para acomodar o processo de fabrico escolhido para as peças foram tomadas várias decisões durante o design, tais como:
- Peças com perfil que permita a separação do macho de areia em processos de fundição.
- Peças com pelo menos 1 plano de simetria para maior facilidade de fabrico em fundição
- Adição de filets para acomodação das limitações do fabrico.

Fig.26, 27 e 28-Considerações de Design for Manufacturing

Especificações finais do braço robótico

O braço robótico completo apresenta as seguintes características:
- Massa de 25 Kg
- 7 graus de liberdade
- Capacidade de carga de 5 Kg
- Raio de serviço entre 1m e 1,5m.
- Comprimento total de 1.6 m
- Material usado- Liga de titânio Ti-6Al-4V cast.
Assim sendo, considera-se que o braço cumpre com os requisitos propostos.


Fig.29-Montagem final


Fig.30-Demonstração dos graus de liberdade.

Conclusões

Em suma, com este projeto, foi possível aprender as diferentes fases que compõem um projeto e desenvolver competências para usar em futuros projetos.
Acredita-se também que este projeto foi bem-sucedido e que poderia avançar à fase de prototipagem, sendo que os requisitos foram cumpridos e que podem ainda ser feitos testes para validação dos mesmos.


Desenho técnico dos vários componentes


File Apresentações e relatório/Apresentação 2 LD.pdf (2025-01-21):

# Laboratório de Design


# Braço Robótico: Infinity Gauntlet

Diogo Ribeiro | 108217
Magner Gusse | 110180

Titã; Objetivos; Conceitos; Next Steps 03; Tópicos a apresentar; Breve introdução sobre a lua de Saturno; Mission statement e requisitos a cumprir no projeto; Conceitos explorados para desenvolvimento da solução; Explicar a próxima fase do projeto

Titã; A maior lua de Saturno

Introdução a Titã; atmosfera substancial.

Titã é um planeta extraordinário. Entre as mais de 150 luas conhecidas no nosso sistema solar, é a única que apresenta uma

Além da Terra, Titã é o único lugar onde podemos encontrar líquidos na forma de rios, lagos e mares para além da sua superfície.

# Principais características de Titã

Habitabilidade; Condições atmosfericas; e climatericas

Estudos indicam que Titã é dos
planetas mais habitaveis do
Sistema Solar.

A atmosfera desta lua é tão densa que
um fato de pressão não seria necessário.
No entanto é necessario ter atenção às
temperaturas extremamente baixas.

# Assuntos a estudar numa missão a Titã

Mapear a superficie; Existência de vida; de Titã; Mapear as diferentes partes; Estudar se já existe vida em; Titã

Constituição
quimica
Estudo dos elemento que
fazem parte da composição

Planeamento da missão; Inicio da missão; Missão terá início em 2027; Chegada a Titã; Colocar o equipamento em Titã em 2034; Custo da missão A missão no seu total custará 1000 milhões de dolares, sendo 400 milhões para desenvolver o braço

Product description; Key Goals; Saturno.; Mission Statement

Estudo da possibilidade de colonização e mineração do planeta Pick and collect de amostras de gelo em Titã

Braço robótico que perfura o gelo para estudo das condições da maior lua de

Mission Statement; Empresas Energéticas; Comunidade ciêntífica; Comunidade Geral; Mercado Principal; Mercado Secundário

- Recorrente a mesma fonte energética do rover

# Requisitos e Especificações

Controlo remoto; Temperaturas entre 89,5 K e 94,5K e substancias ácidas

Acoplamento ao
Rover simples
Deve ser feito em 30
minutos
Resistência às
condições

Controlado pela ground
station na Terra
Adaptação à
gravidade

Aceleração gravítica com
um valor de 1,352 m/s^2

Perfuração da superfície; Fiabilidade; Coleção de amostras; Mobilidade; Requisitos e especificações; Amostras de 41mm de diametro e 500mm de profundidade; Capacidade de carga de pelo menos 5 Kg; Tempo de vida de 10 anos Manutenção ao fim de 5 anos; Pelo menos 5 graus de liberdade

03


# Geração de Conceitos

Conceitos pensados para a
solução

# Geração de Conceitos


## Benchmarking

Geração de Conceitos; Controladores; Que irão ditar aos atuadores, os movimentos a seguir pelos motores e outros atuadores

Geração de Conceitos; Elos de ligação; Efetuam a ligação entre elementos do braço e dos atuadores.

# Geração de Conceitos


## Atuadores

Os elementos que geram os movimentos, tanto de rotação como de translação do braço robótico

# Geração de Conceitos

## Broca Oca

O elemento mais importante, que irá realizar a perfuração do gelo e coleção da amostra.

# Geração de Conceitos


Juntas; Revestimento; Atuadores; Coleção de amostra; Uso maioritário de atuadores elétricos; Características do braço; Para movimento em 3 eixos na base, para movimento da broca e juntas rotativas em outras zonas; Filme para proteção contra substâncias acidas presentes; Amostra coletada com recurso a broca e ventosa; Sensores Sensores de posição e proximidade

# Conceito preliminar

Conceito preliminar a ser
desenvolvido nas próximas
fases do projeto

# Conceito preliminar

## Detalhes


A base de fixação ao rover

# Conceito preliminar

## Detalhes


Um dos elementos do braço
robótico

# Conceito preliminar

## Detalhes


Outros elementos do braço

# Conceito preliminar

## Detalhes

Broca oca que faz a perfuração e coleção das amostras de gelo

# Imagem conceptual


Slidesgo (http://bit.ly/2Tynxth) | Flaticon (http://bit.ly/2TyoMsr)

Freepik (http://bit.ly/2TtBDfr)

CREDITS: This presentation template was created by Slidesgo, (http://bit.ly/2Tynxth) including icons by Flaticon, (http://bit.ly/2TyoMsr) and infographics & images by Freepik (http://bit.ly/2TtBDfr)

# Obrigado!

Dúvidas?

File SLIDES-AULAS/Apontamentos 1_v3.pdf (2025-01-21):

03/10/2023

1

Laboratório de Design
Paulo Lima| Ricardo Torcato

# Laboratório de design

Laboratório de Design
Paulo Lima| Ricardo Torcato

## Objetivos

A. Desenvolver a capacidade de design num contexto de desenvolvimento de produto para o setor aeroespacial.
B. Reconhecer e aplicar metodologias de desenvolvimento de novos produtos no setor aeroespacial.
C. Reconhecer, selecionar e aplicar as tecnologias de fabrico, técnicas e materiais no contexto da indústria aeroespacial.
D. Adquirir competências para realizar o desenvolvimento integrado de design e manufatura de produto, no contexto da indústria aeroespacial.
E. Utilizar modelos e protótipos para apoio ao desenvolvimento e comunicação de produto.

2

Laboratório de Design
Paulo Lima| Ricardo Torcato

## Conteúdos

### 1. Design e desenvolvimento de produto

- Metodologias estruturadas de desenvolvimento de produto
- Design Sustentável

### 2. Projeto integrado de design e manufatura de produto no contexto do setor aeroespacial

- Desenvolvimento conceptual
- Processos de seleção de tecnologias de fabrico
- Comunicação do projeto

### 3. Modelos e protótipos

- Maqueta, modelo e protótipo
- Seleção de materiais e tecnologias
- Técnicas de prototipagem manuais e oficinais

Laboratório de Design
Paulo Lima| Ricardo Torcato

## Avaliação

Época Normal/Recurso: 100% Trabalho prático laboratorial

## Bibliografia recomendada

Product Design and Development, Karl T.Ulrich, Steven Eppinger, McGraw-Hill,2020 Introduction to Aircraft Design, John P. Fielding, Cambridge University Press, 2017 Introduction to Aerospace Structures and Materials, René Alderliesten, TU Delft Open, 2018
Aircraft Design: A Conceptual Approach, Daniel P. Raymer, AIAA Education Series, 2018
Design and Development of Aircraft Systems, Allan Seabridge, Ian Moir, Wiley, 2020
Aircraft Structures for Engineering Students, T. H. G. Megson, ELSEVIER SCIENCE & TECHNOLOGY, 2017

3

Laboratório de Design
Paulo Lima| Ricardo Torcato

## https://www.youtube.com/watch?v=5qqsMjy8Rx0

Laboratório de Design
Paulo Lima| Ricardo Torcato

## Trabalho: Braço Robótico para acoplamento a Rover espacial destinado a exploração de planetas

4

Laboratório de Design


Paulo Lima| Ricardo Torcato | https://www.youtube.com/watch?v=5qqsMjy8Rx0

## NASA's Perseverance Mars Rover: Mission Overview:

https://www.youtube.com/watch?v=-TGH3--21_ghttps://mars.nasa.gov/mars2020/

Mars Sample Return

Landed on February , 2021.

Laboratório de Design


Paulo Lima| Ricardo Torcato

## 3D visualization

https://mars.nasa.gov/mars2020/spacecraft/rover/

## NASA's Perseverance Mars Rover: Mission Overview:

5

Laboratório de Design
Paulo Lima| Ricardo Torcato

### Tools on the Perseverance Rover

The Perseverance rover has tools to study the history of its landing site, seek signs of ancient life, collect rock and soil samples, and help prepare for human exploration of Mars. The rover carries:

CAMERAS & SPECTROMETERS
- Mastcam-Z
- PIXL (Planetary Instrument for X-ray Lithochemistry)
- SHERLOC (Scanning Habitable Environments with Raman & Luminescence for Organics & Chemicals)
- SuperCam

GROUND-PENETRATING RADAR
- RIMFAX (Radar Imager for Mars' Subsurface Experiment)

ENVIRONMENTAL SENSORS
- MEDA (Mars Environmental Dynamics Analyzer)

TECHNOLOGY DEMO
- MOXIE (Mars Oxygen ISRU Experiment)

SAMPLE COLLECTION
- Coring Drill
- Sample Handling System
https://mars.nasa.gov/mars2020/mission/status/


Laboratório de Design

Paulo Lima| Ricardo Torcato https://mars.nasa.gov/mars2020/spacecraft/rover/arm/

6


Laboratório de Design
Paulo Lima| Ricardo Torcato

## Mars Curiosity Rover

Launch: November, 2011

https://mars.nasa.gov/msl/home/

Landed: Aug., 2012

Laboratório de Design
Paulo Lima| Ricardo Torcato

## Instruments on the Mars Exploration Rovers

https://mars.nasa.gov/mer/mission/overview/https://mars.nasa.gov/mer/

## Mars Exploration Rover

## Spirit and Opportunity: Twin Mars Exploration Rovers

landed on Mars January 3 and January 24, 2004

7

Laboratório de Design
Paulo Lima| Ricardo Torcato

## Perguntas a fazer numa primeira fase do projeto o que é um Rover? o que é um rover para exploração planetária? o que é um braço robótico? o que é um braço robótico para exploração espacial?

## Trabalho

## Benchmarking Competitivo Produtos relacionados

Laboratório de Design
Paulo Lima| Ricardo Torcato

O que é um Braço Robótico?
Funções; tipologias, cinemática; constituição de braços robóticos

Simulação e otimização estrutural • design convencional • design generativo

Teste Laboratorial • 1 ou mais componentes que constituem o braço robótico

Desenho Mecânico
- design para tecnologias convencionais • design para AM

Protótipo

Mission Statement do projeto: seleção do planeta a explorar,…

## Trabalho

Desenvolvimento

8

Laboratório de Design

Paulo Lima| Ricardo Torcato | Product Design and Development, Karl T.Ulrich, Steven Eppinger, McGraw-Hill,2020

## Metodologias de Desenvolvimento de Produto 6 fases de um processo genérico de desenvolvimento de produto

Laboratório de Design
Paulo Lima| Ricardo Torcato

## Fase 0 Precede a aprovação do projeto e lançamento do processo de desenvolvimento de

produto.

## Tem por objetivo (output) definir um Mission Statement do projeto, alinhado com a

estratégia corporativa da empresa.

## Metodologias de Desenvolvimento de Produto

## O que é que constitui um mission statement? Documento que define o mercado alvo para o produto, os objetivos de negócio e os

pressupostos e restrições a cumprir no processo de desenvolvimento.

## Especifica uma direção a seguir mas não deve definir um destino específico ou uma forma particular de atuação

9

Laboratório de Design
Paulo Lima| Ricardo Torcato

## Mission Statement

## Pode incluir

- Brief ( uma frase) com a descrição do produto referindo quais são os benefícios para o cliente

## - Objetivos chave do negócio – data para lançamento do produto no mercado; performance financeira,… - Mercado Alvo – primário e secundário - Pressupostos e Restrições - que permitam garantir um processo de desenvolvimento de

produto eficaz ( sem ser generalista).
- Stakeholders – identificação de todos as partes interessadas (influenciadas pelo produto)
- end users
- sales force
- production department
- service department, etc.

Laboratório de Design
Paulo Lima| Ricardo Torcato

Product Description
•A hand-held, power-assisted device for installing threaded fasteners Key Business Goals
•Product introduced in 4th Q of 2000
•50% gross margin
•10% share of cordless screwdriver market by 2004 Primary Market
•Do-it-yourself consumer
Secondary Markets
•Casual consumer
•Light-duty professional
Assumptions
•Hand-held
•Power assisted
•Nickel-metal-hydride rechargeable battery technology Stakeholders
•User
•Retailer
•Sales force
•Service center
•Production
•Legal department

## Mission Statement

## Aparafusadora

10

Laboratório de Design Paulo Lima| Ricardo Torcato; Fase 1 – Desenvolvimento de Conceitos; Perform Economic Analysis; Benchmark Competitive Products; Build and Test Models and Prototypes; Identify Customer Needs; Establish; Target; Specifications; Generate Product Concepts; Select Product Concept(s); Set Final Specifications; Plan Downstream

Product Design and Development, Karl T.Ulrich, Steven Eppinger, McGraw-Hill,2020

Development Test Product Concept(s) Mission Statement

Laboratório de Design
Paulo Lima| Ricardo Torcato

## Identificação de Necessidades

## Recolha da informação diretamente no consumidor

## - Entrevistas - Sessões de trabalho em grupo - Observação direta do produto em uso

## Tradução das necessidades em requisitos/atributos

## - Expressar as necessidades em termos do que o produto deve fazer e não como o vai fazer - Utilizar frases afirmativas

11

Laboratório de Design
Paulo Lima| Ricardo Torcato
Guideline | Customer Statement | Attribute Statement-Wrong | Attribute Statement-Right What Not How

# Specificity Positive Not Negative Attribute of the Product Avoid “Must” and “Should

“Why don’t you put protective shields around the battery contacts?”

“I drop my screwdriver all the time.”

“It doesn’t matter if it’s raining, I still need to work

outside on Saturdays.”

“I’d like to charge my battery from my cigarette lighter.”

“I hate it when I don’t know how much juice is left in the

batteries of my cordless
tools.”

The screwdriver battery
contacts are covered by a
plastic sliding door.

The screwdriver battery is protected from accidental
shorting.

The screwdriver is rugged. The screwdriver operates normally after repeated

dropping. The screwdriver is not disabled by the rain.
| The screwdriver operates normally in the rain.

An automobile cigarette
lighter adapter can charge the screwdriver battery.

The screwdriver battery
can be charged from an
automobile cigarette
lighter. The screwdriver should provide an indication of the

energy level of the battery.

The screwdriver provides
an indication of the energy level of the battery.

## Identificação de Necessidades Traduzir a necessidade num atributo/requisito do produto

Laboratório de Design
Paulo Lima| Ricardo Torcato

## Definição de especificações Os requisitos são estabelecidos de forma qualitativa e são úteis para desenvolver uma perspetiva clara das questões relevantes para o cliente, e que o design e engenharia devem dar resposta. Deixam contudo uma margem subjetiva demasiado grande para a

equipa que irá desenvolver o produto.

## As especificações são uma descrição precisa e mensurável do que o produto tem que fazer ou cumprir, mas não devem dizer qual a solução para garantir o seu

cumprimento.
por exemplo:
a suspensão de uma bicicleta deve ser fácil de instalar (requisito)
o tempo médio para instalação da suspensão deve ser inferior a 60 segundos (especificação)

Especificação é constituída por uma métrica, unidade de medida e por um valor ( valor absoluto,

## gama de valores;….): - métrica tempo médio para instalação da suspensão - Valor/unidade de medida: < 60 segundos

12

Laboratório de Design
Paulo Lima| Ricardo Torcato


## - Primários (Estratégicos) • Secundários (Táticos) • Terciários (Operacionais)

## Estruturação e priorização dos requisitos

Primários: oito dimensões da qualidade, por David A.Garvin

Desempenho: Características básicas de funcionamento (ex: Automóvel – aceleração, velocidade e conforto). Fiabilidade: Probabilidade de funcionamento inadequado ou falha de um

produto num determinado intervalo de tempo. Conformidade: Conformidade com as especificações pré-estabelecidas. Durabilidade: Tempo de vida antes da sua deterioração e substituição (ex:

tempo de vida de uma lâmpada). Estética: Aparência, aroma, sabor.

Serviço pós-venda: Tempo e facilidade de reparação, competência da reparação, pontualidade e cortesia no serviço pós-venda. …… https://abepro.org.br/biblioteca/tn_sto_212_257_26747.pdf

Laboratório de Design
Paulo Lima| Ricardo Torcato

1- Requisitos obrigatórios ou necessários (o que o cliente precisa)
Atributos do produto obrigatórios. Corresponde a uma necessidade básica do cliente.
Se este requisito existir, não irá necessariamente satisfazer o cliente. Por outro lado, a sua ausência levaria a uma verdadeira insatisfação. Um telefone que não faz nem recebe chamadas…….

2- Requisitos unidimensionais ou desempenho (o que cliente deseja)
Responde a uma necessidade de desempenho do produto. Traz satisfação aos clientes quando está presente e quanto maior o seu desempenho, mais satisfeitos estarão. Se não existir, também pode causar decepção.
Exemplo: Um carro responde à necessidade de locomoção e funciona normalmente, mas o cliente estará à espera por exemplo de baixos consumos (eficiência energética) ou de uma potência que permita fáceis ultrapassagens,……

3- Requisitos Atrativos (o que encanta o cliente)
Atributos do produto inesperados que geram encanto no cliente, tornando-o extremamente satisfeito pela diferença que oferecem relativamente a outros produtos da concorrência. A sua inexistência não gera insatisfação.

Por exemplo: num automóvel, um sistema de som de alta qualidade ou dados de internet gratuitos.

4- Requisitos Indiferentes (não afetam o grau de satisfação do cliente)
Atributos do produto que não afetam o grau de satisfação do cliente, independentemente do seu desempenho ou da sua existência. Cor dos cabos elétricos ou da cor/geometria do material de isolamento acústico debaixo do capot,….

5- Requisitos Reversos (o que desencanta o cliente)
Exemplo: durabilidade de uma bateria abaixo do esperado

## Modelo de Kano

13

Laboratório de Design
Paulo Lima| Ricardo Torcato

1- Requisitos obrigatórios ou necessários (o que o cliente precisa)
2- Requisitos unidimensionais ou desempenho (o que cliente deseja) 3- Requisitos Atrativos (o que encanta o cliente)
4- Requisitos Indiferentes (não afetam o grau de satisfação do cliente) 5- Requisitos Reversos (o que desencanta o cliente)

## Modelo de Kano


Laboratório de Design
Paulo Lima| Ricardo Torcato


## Requisitos

Exemplo – suspensão frontal de uma bicicleta de BTT

14

Laboratório de Design
Paulo Lima| Ricardo Torcato

## Definição de especificações

## Definição das especificações

## 1. Preparar a lista de métricas 2. Benchmarking competitivo 3. Estabelecer valores alvo ideais e marginais 4. Refletir sobre resultado e sobre o processo

Laboratório de Design
Paulo Lima| Ricardo Torcato

## Benchmarking

Fornece uma perspetiva externa sobre as oportunidades de melhoria de produtos, tecnologias,

## fabrico,….) Benchmarking competitivo - comparação entre os concorrentes e com os concorrentes, com o

objetivo de identificar pontos fortes e fracos e retirar conclusões sobre o produto que se pretende

## desenvolver (funcionalidades, especificações,….)

## Etapas de um Benchmarking - Definir os principais players/concorrentes (mínimo de 3) - Definir as métricas a analisar - Contactar com clientes com o objetivo de melhor aferir o desempenho dos produtos - Registar e analisar os dados recolhidos

15


Laboratório de Design
Paulo Lima| Ricardo Torcato

## Exemplo – suspensão frontal de uma bicicleta de BTT

Laboratório de Design
Paulo Lima| Ricardo Torcato


Matriz de requisitos-métricas Referência: Product Design and Development, Karl T.Ulrich, Steven Eppinger, McGraw-Hill

16

Laboratório de Design
Paulo Lima| Ricardo Torcato


## Benchmarking competitivo baseado nas

métricas Referência: Product Design and Development, Karl T.Ulrich, Steven Eppinger, McGraw-Hill

Laboratório de Design
Paulo Lima| Ricardo Torcato


## Benchmarking competitivo baseado nas métricas

(continuação) Referência: Product Design and Development, Karl T.Ulrich, Steven Eppinger, McGraw-Hill

17

Laboratório de Design
Paulo Lima| Ricardo Torcato


Especificações Alvo Referência: Product Design and Development, Karl T.Ulrich, Steven Eppinger, McGraw-Hill

Laboratório de Design
Paulo Lima| Ricardo Torcato

## Grupos de trabalho - Pedro Moura e Júlia Pereira - Luiza Pessoa e Bruna Santos - Diogo Ribeiro e Magner Gusse - Léane Marques e Nuno Pereiro

18

Laboratório de Design; Paulo Lima| Ricardo Torcato; Perform Economic Analysis; Benchmark Competitive Products; Build and Test Models and Prototypes; Identify Customer Needs; Establish; Target; Specifications; Generate Product Concepts; Select Product Concept(s); Set Final Specifications; Plan Downstream; Development Mission Statement; Test Product Concept(s); Development Plan Geração de Conceitos

Laboratório de Design
Paulo Lima| Ricardo Torcato

## Geração de Conceitos Fase 1- Clarificar o problema

- Decompor um problema complexo em subproblemas mas simples - Decomposição Funcional
- Focar os esforços iniciais em subproblemas mais críticos

Dividir a função em subfunções

Exemplo: agrafador

19

Laboratório de Design
Paulo Lima| Ricardo Torcato

## Geração de Conceitos

## Fase 2- Procurar externamente

- Entrevistar lead users
- Consultar especialistas
- Procurar patentes
- Procurar na literatura
- Benchmark de produtos diferentes mas com funcionalidades semelhantes

## Fase 3- Procurar internamente

- Sessões individuais ou de grupo

Laboratório de Design
Paulo Lima| Ricardo Torcato


## Geração de Conceitos

## Fase 4- Exploração sistemática

Como resultado da pesquisa externa e interna a equipa recolheu dezenas ou centenas de soluções para subproblemas.

20

Laboratório de Design
Paulo Lima| Ricardo Torcato

## Geração de Conceitos

## Fase 4- Exploração sistemática


Como resultado da pesquisa externa e interna a equipa recolheu dezenas ou centenas de soluções para subproblemas.

- Árvore de classificação e conceitos
- Combinação de conceitos
- ……

Laboratório de Design Paulo Lima| Ricardo Torcato; Geração de Conceitos; Fase 4- Exploração sistemática; Árvore de classificação e conceitos; Para abordagens diferentes, assignar equipas diferentes para explorar um conjunto de soluções.; aplicação pretendida: perigosidade; complexidade técnica para implementar a solução,…..

Tomar decisões relativamente a alguns dos ramos. Eliminar ou descartar pela falta de adequação à

21


Laboratório de Design
Paulo Lima| Ricardo Torcato

## Fase 4- Exploração sistemática

. Refinamento da decomposição do problema para um ramo particular

Laboratório de Design
Paulo Lima| Ricardo Torcato

## Fase 4- Exploração sistemática

. | Sub-problema

## Soluções alternativas

22

Laboratório de Design
Paulo Lima| Ricardo Torcato

## Fase 4- Exploração sistemática

. Combinação de conceitos


Laboratório de Design
Paulo Lima| Ricardo Torcato

## Fase 4- Exploração sistemática

. Combinação de conceitos


## Seleção de Conceitos Teste de Conceitos

Paulo Lima| Ricardo Torcato; Product Design and Development, Karl T.Ulrich, Steven Eppinger, McGraw-Hill,2020; Especificações finais …..; concept generation; concept screening; concept scoring; concept testing

Laboratório de Design

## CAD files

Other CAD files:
Entrega final do projeto/Ombro1.SLDDRW

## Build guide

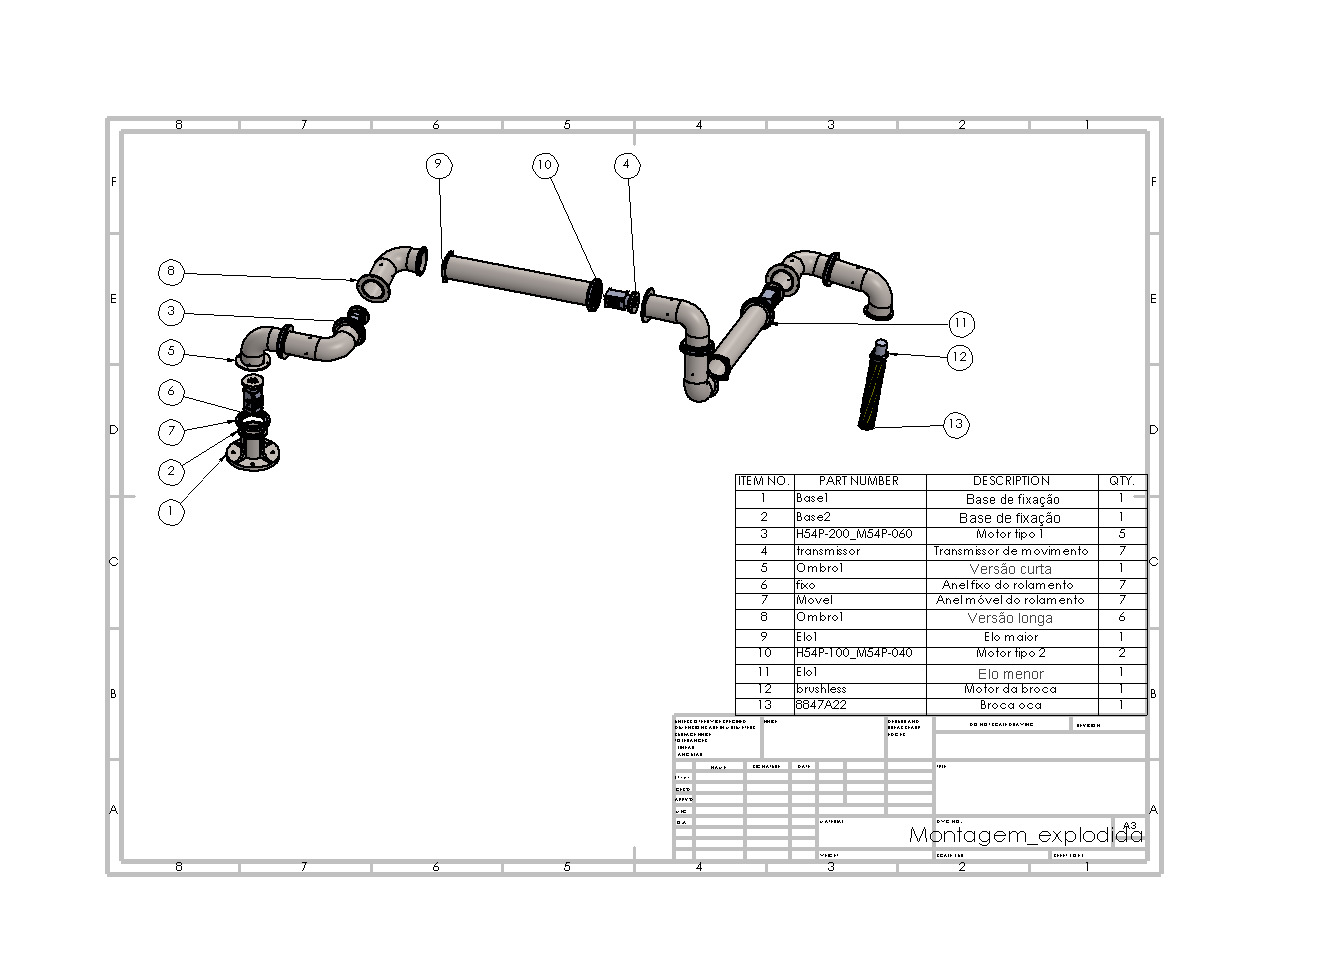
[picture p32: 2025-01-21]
Entrega final do projeto/Montagem_explodida.JPG

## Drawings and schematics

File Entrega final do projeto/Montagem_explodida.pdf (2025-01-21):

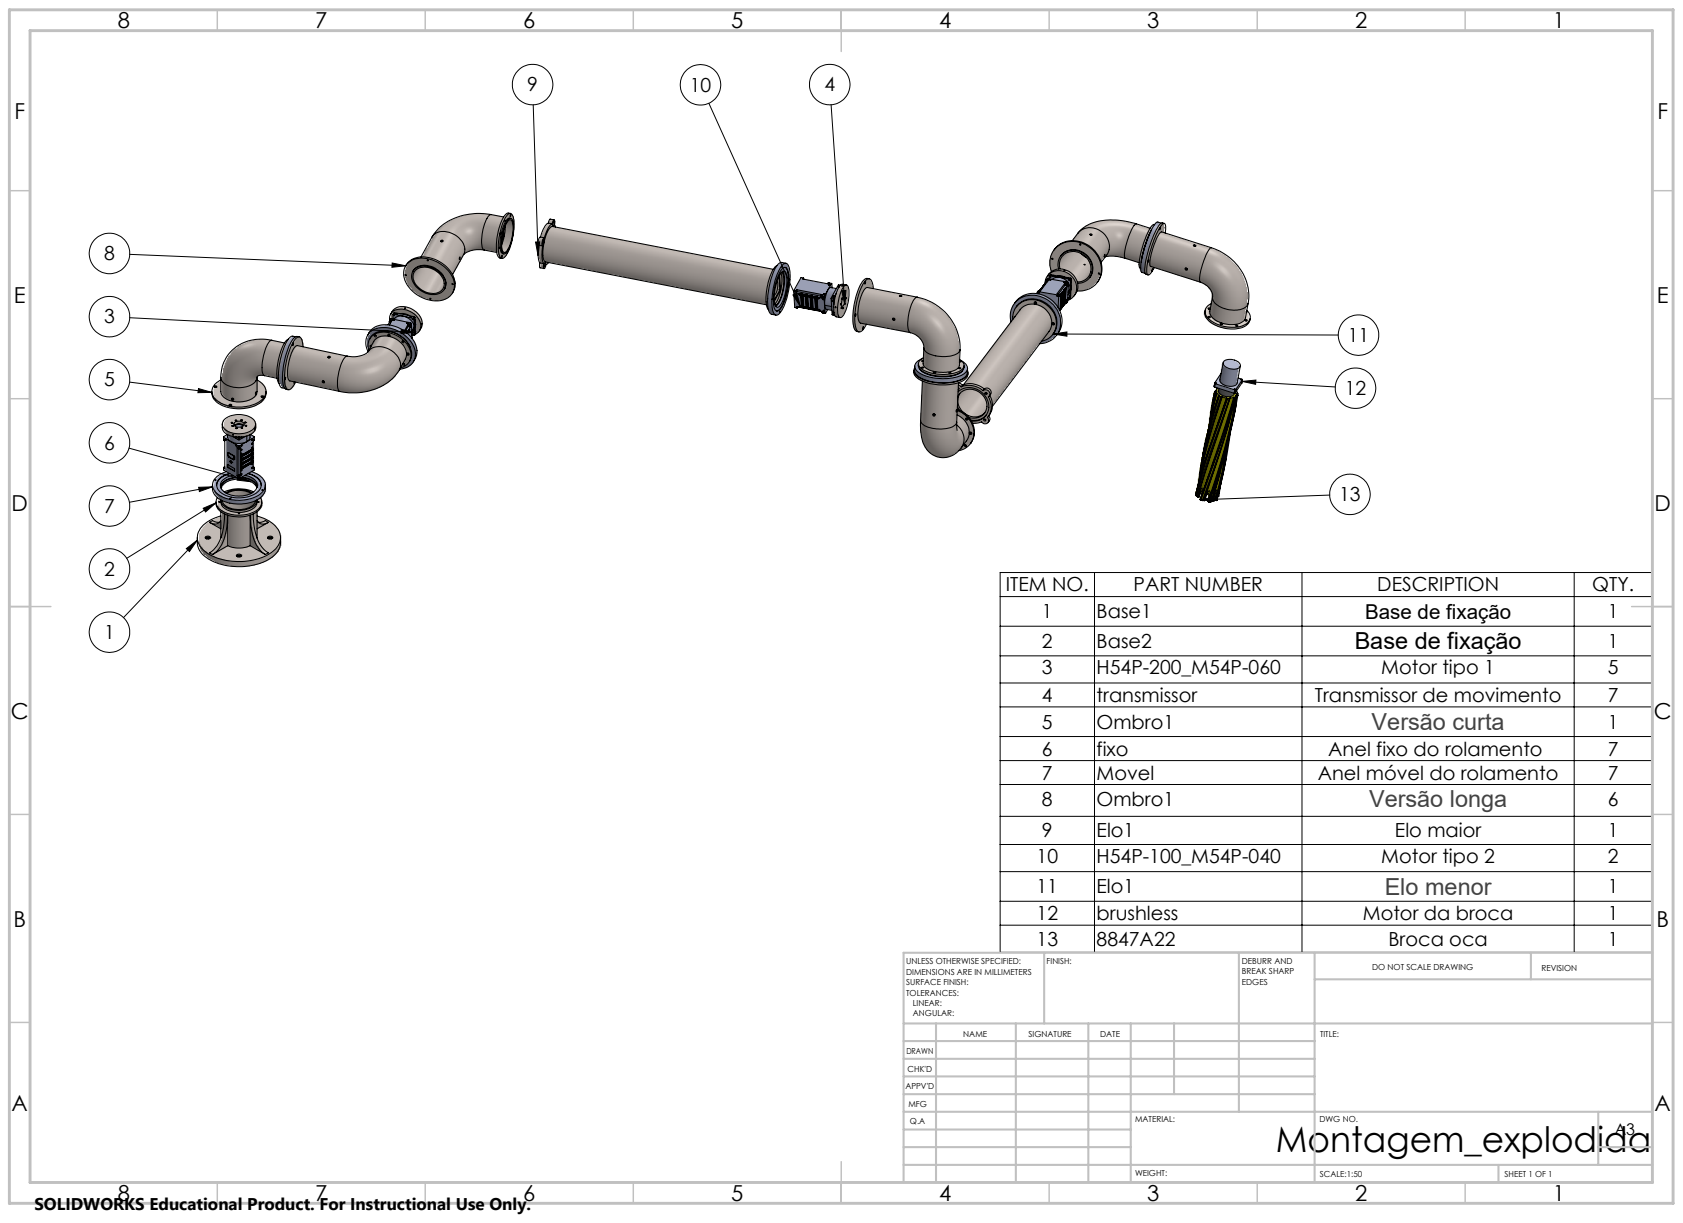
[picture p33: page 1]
Elo1; Elo maior; SCALE:1:50; SHEET 1 OF 1

ITEM NO. | PART NUMBER | DESCRIPTION | QTY.
1 | Base1 | Base de fixação | 1
2 | Base2 | Base de fixação | 1
3 | H54P-200_M54P-060 | Motor tipo 1 | 5
4 | transmissor | Transmissor de movimento | 7
5 | Ombro1 | Versão curta | 1
6 | fixo | Anel fixo do rolamento | 7
7 | Movel | Anel móvel do rolamento | 7
8 | Ombro1 | Versão longa | 6

10 | H54P-100_M54P-040 | Motor tipo 2 | 2
11 | Elo1 | Elo menor | 1
12 | brushless | Motor da broca | 1
13 | 8847A22 | Broca oca | 1

UNLESS OTHERWISE SPECIFIED: DIMENSIONS ARE IN MILLIMETERS SURFACE FINISH: TOLERANCES: LINEAR: ANGULAR: | FINISH: | DEBURR AND BREAK SHARP EDGES | DO NOT SCALE DRAWING | REVISION

NAME | SIGNATURE | DATE | | | | TITLE:

DRAWN
CHK'D
APPV'D
MFG
Q.A | | | | MATERIAL: Montagem_explodida | DWG NO. | A3

SOLIDWORKS Educational Product. For Instructional Use Only.
